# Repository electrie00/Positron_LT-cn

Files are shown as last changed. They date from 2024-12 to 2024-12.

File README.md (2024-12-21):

<div align="center">
  
# Positron LT-cn

<br>
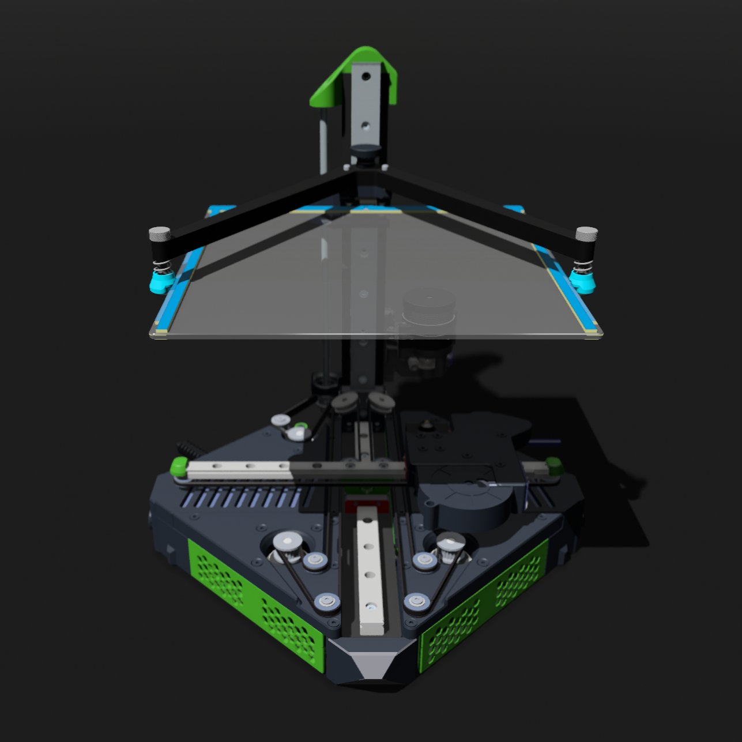
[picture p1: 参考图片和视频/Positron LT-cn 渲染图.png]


<br>

</div>

<br>

<br>

1. 国内可制造，任何零件均可在国内买到
2. 价格合理，目前价格大约在1500~2000元左右
3. 原版 LT 用户也可以很容易的升级这个版本，解决 LT 原版的问题
   
<br>

## - 改动点   （添加了部分 Positron V3.2 的新设计）： 

  1. **后惰轮张紧块** —— LT 原版的张紧块使用4个小惰轮倾斜安装，无法承受皮带张紧力，会被逐渐拉歪，最终导致皮带脱轨。 使用 V3.2 的设计两个大惰轮可以很好的解决这个问题，需要注意的是，V3.2 的惰轮是 CNC 做的，而此改版 LT 使用的是与 V3.2 参数相似成品惰轮，淘宝有卖

  2. **挤出机** —— LT 原版挤出机基于 BMG，我实际使用时有明显挤出不足的问题。使用 V3.2 的 Orbiter2.0 挤出机，仅修改了安装孔位，内部挤出结构与 v3.2 保持一致。 同时扩大了 RGB 灯孔位，以便折叠时刚好把挤出机卡入凹槽

  3. **热床接口** —— lt原版热床的磁吸接口强度不够，有时连接不稳，再加上 LT 原版热床支架的热床夹持结构不稳。整个热床可以说是摇摇欲坠。一旦磁吸接口虚接产生火花，就会导致热床接口损坏（ 亲身经历 ）。  使用 V3.2 的金手指连接接口，非常稳固。以及 V3.2 的热床支架，体积更小，夹持更稳，调平也更方便（ LT 原版的调平螺丝在下面，很别扭 ）。  需要注意的是，准确来说此改版lt仅使用了金手指接口，并没有 PCB，因此安装需要依赖胶水固定，以及接线需要做好绝缘，因为接线点与线轨金属滑块紧贴，容易短路

  4. **ITO 热床** —— ITO导电玻璃，整块玻璃均导电，发热更加均匀。两根长导线连接热床对边边缘作电极，分别连接 24V 正负极便可发热，中间区域是完全透明的整块玻璃。使用淘宝购买 ITO 玻璃加上可在嘉立创制作的 PCB，便可自制，这样就不用去国外买热床了，自己做的价格其实比淘宝的成品热床便宜。不建议使用淘宝的成品热床，那个并不是 ITO 热床，而是普通的导线粘贴在玻璃上。这个导线会干扰 Positron 的红外调平模块（ IR Probe ），导致有大量死区无法触发限位，影响 Z 归位以及网床探测

  5. **主体框架** —— 原版LT使用1010型材搭建框架，但这个在国内是买不到的，基本可以说没有办法。此改版 LT 修改为整体 CNC，价格还行 300 以内吧，这也是没有办法
  
  6. **皮带固定块** —— LT 原版的皮带固定块，仅仅靠设计的弯曲凹槽卡入皮带固定，也就是仅靠摩擦力固定，但凡皮带张紧一点，皮带便会脱落。而 V3.2 的皮带固定块改动太太，无法移植，并且 V3.2 的固定块设计也不算优秀。所以此改版 LT 在原版固定块基础上增加了 0.5mm 小孔，可以使用 0.5mm 的钢针插入，将皮带和固定块串在一起，就像串烧烤一样
     
<br>

## - 与 LT 版本和 V3.2 版本相比

 1. 用 CNC 解决了 LT 1010铝型材买不到的问题，同时添加了 V3.2 的新设计，也改进了大部分 LT 的 bug，使用体验大幅上升
 2. 比 V3.2 容易制造，至少不存在买不到特殊零件的问题了，并且是lt集成电源的,但体积就会比 V3.2 大一些。同时价格也比 V3.2便宜一倍
<br>

## - 注意

  1.此工程的文件仍在整理，文档依然还有许多没写
  
  2.此版本没有为打印机添加触摸屏幕，但保留了原版 LT 安装屏幕的孔位，有需要可以自己参考 LT 安装
  
  3. X，Y，Z 轴的步进电机依然不太好买，具体参数为 42 步进电机20mm厚15mm轴长。而我目前买的电机是 20mm 轴长，装上去才发现高了 5mm 会阻挡打印头移动，目前解决方案是在电机安装孔垫矮了 5mm，便可解决问题。其实也证明轴长 15~20mm 都是可以的，自行添加垫片调整高度即可

<br>

# 感谢Positron LT 和 Position 3D

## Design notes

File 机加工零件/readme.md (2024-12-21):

## 1~3 号文件只能 CNC 加工，嘉立创报价如下

1. Y轴 主梁               90.4元
2. Z轴 主梁               77.84元
3. Y轴-Z轴 折叠处连接块    49.38元
<br>

## 4 号文件按道理也应该 CNC 价格，嘉立创报价如下

4. 底部 X轴 横梁（两件）    93.93 * 2 = 187.86 元

#### 不过这个零件明明是最小的，单价却比前面的 CNC 零件都要贵，而且还需要两件。所以如果嫌贵的话，也可以使用3d打印塑料件替代，反正这两根梁不用承受很大的力，我也是3d打印的这两个零件
<br>

## 5 号文件需要7件，不过这个就不用 CNC 了，有更便宜的解决方法：去淘宝上随便找一家铁板激光切割定制的，将step或dwg图纸发过去，记得告知厚度1.5mm。参考单价如下

5. L形连接板 （七件）        18元

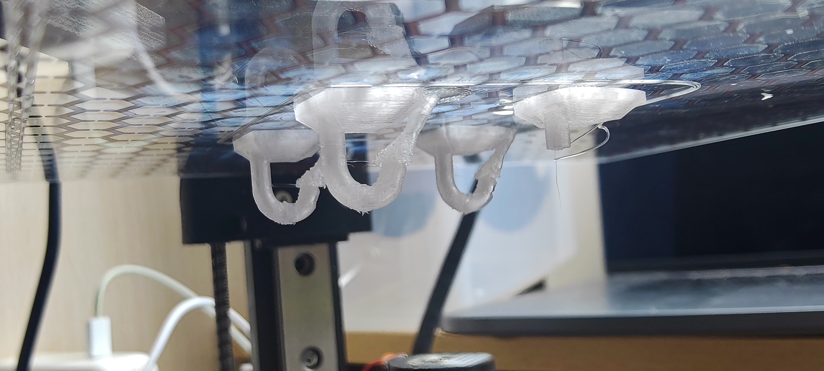
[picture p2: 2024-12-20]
参考图片和视频/透明petg 挂钩(1).jpg

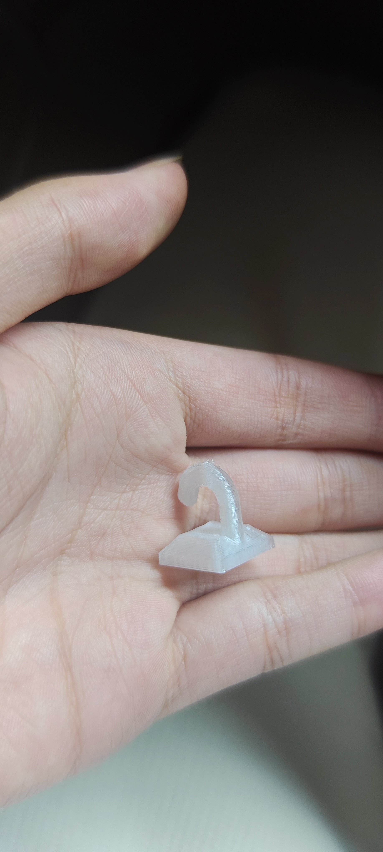
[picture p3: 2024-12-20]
参考图片和视频/透明petg 挂钩 (2).jpg

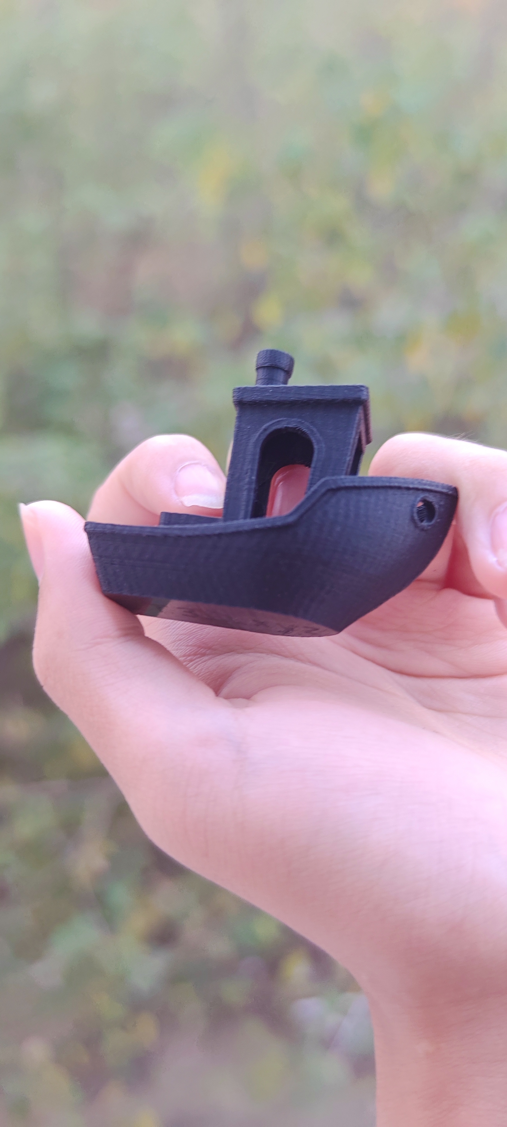
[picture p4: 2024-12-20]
参考图片和视频/测试小船.jpg

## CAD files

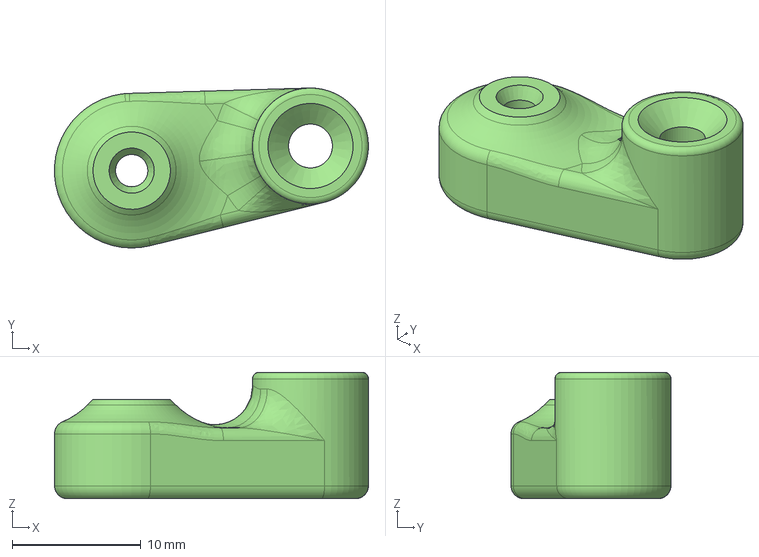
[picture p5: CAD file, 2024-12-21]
打印件/STEP/Z轴皮带张紧调节.step
24.4 x 12.4 x 9.80 mm

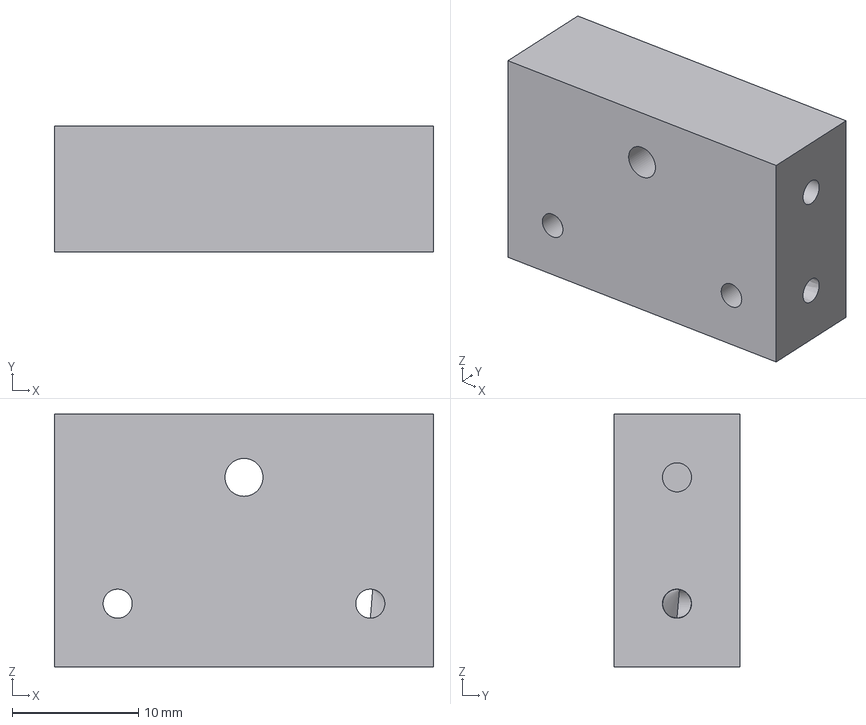
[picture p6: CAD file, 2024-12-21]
机加工零件/3. Y轴-Z轴 折叠处连接块.step
30.0 x 10.00 x 20.0 mm

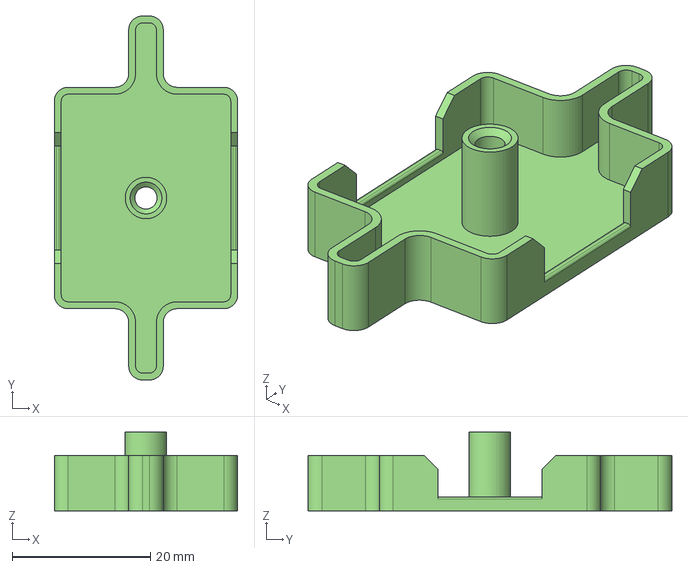
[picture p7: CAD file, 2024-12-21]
打印件/STEP/底盖打印件.step
26.5 x 52.6 x 11.4 mm

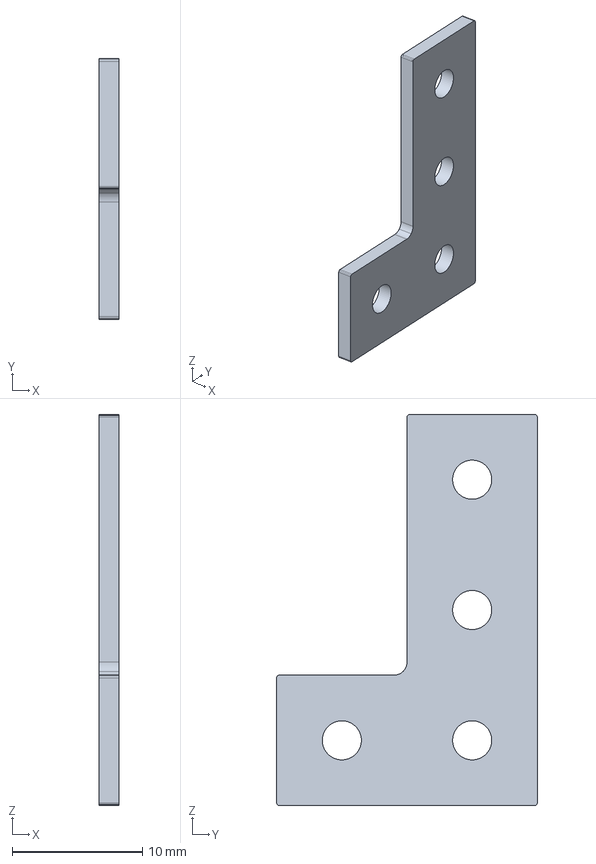
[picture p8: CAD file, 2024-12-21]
机加工零件/5. L形连接板（七件）.step
1.50 x 20.0 x 30.0 mm

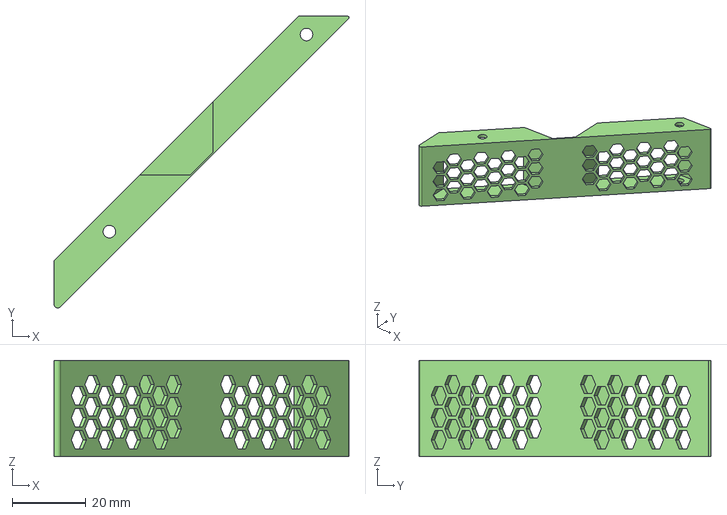
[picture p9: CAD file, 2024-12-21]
打印件/STEP/右装饰挡板.step
79.9 x 79.0 x 26.0 mm

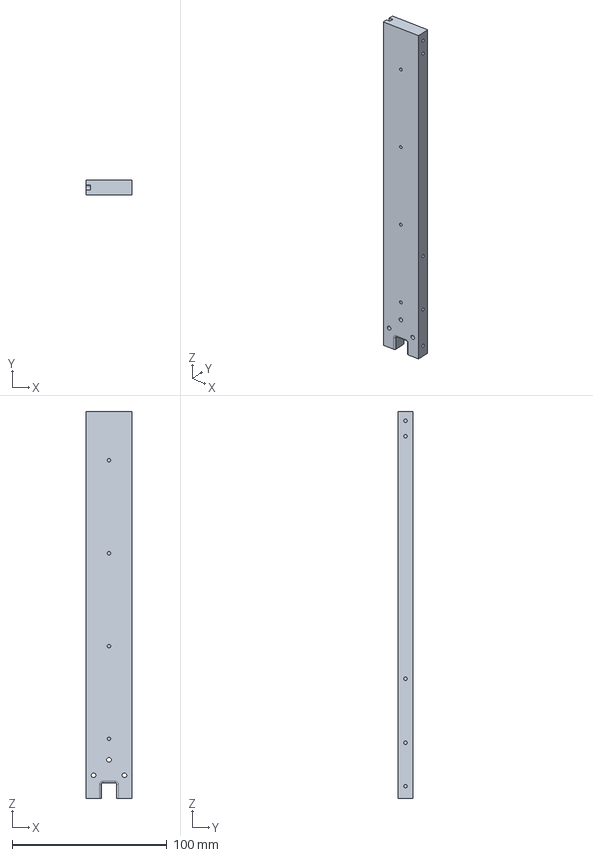
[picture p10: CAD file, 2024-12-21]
机加工零件/2. Z轴 主梁.step
30.0 x 10.0 x 250.0 mm

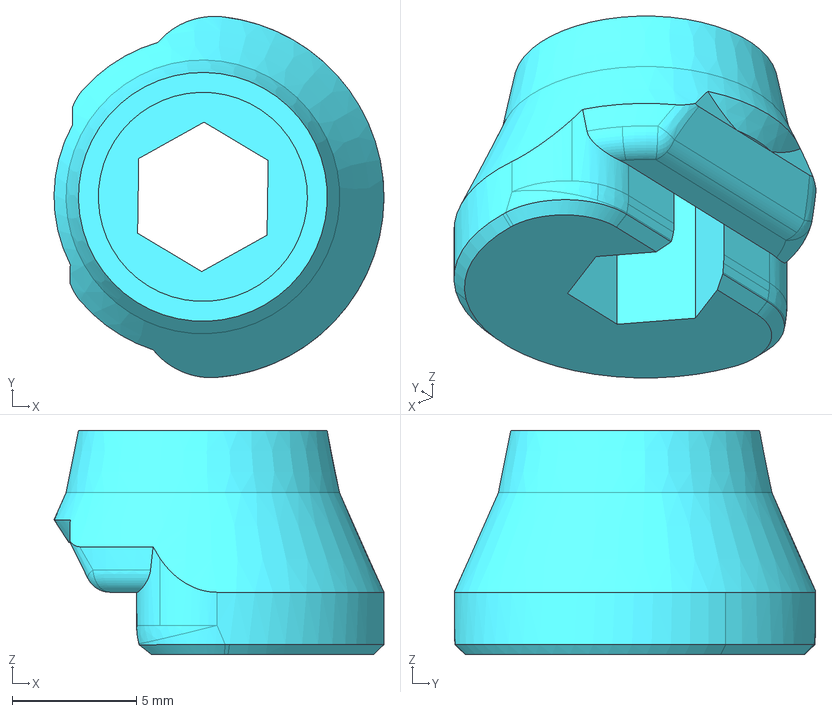
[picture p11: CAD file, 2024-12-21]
打印件/STEP/右端热床夹持打印件.step
13.3 x 14.5 x 9.00 mm

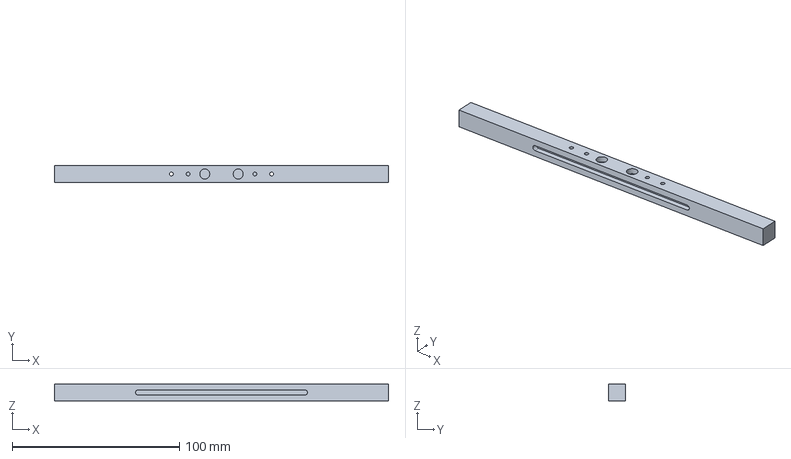
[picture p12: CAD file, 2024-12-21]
机加工零件/4. 底部 X轴 横梁（两件）.step
200.0 x 10.0 x 10.0 mm

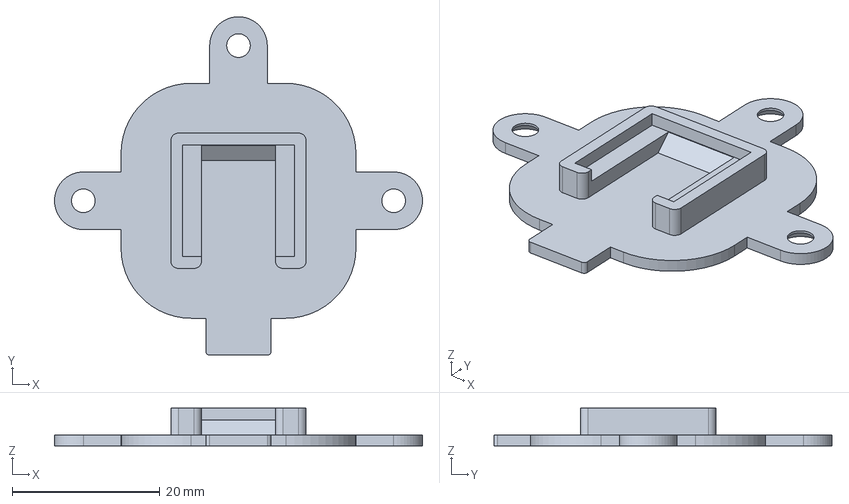
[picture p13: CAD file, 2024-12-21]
打印件/STEP/WS2812 RGB安装板.step
49.8 x 45.8 x 5.10 mm

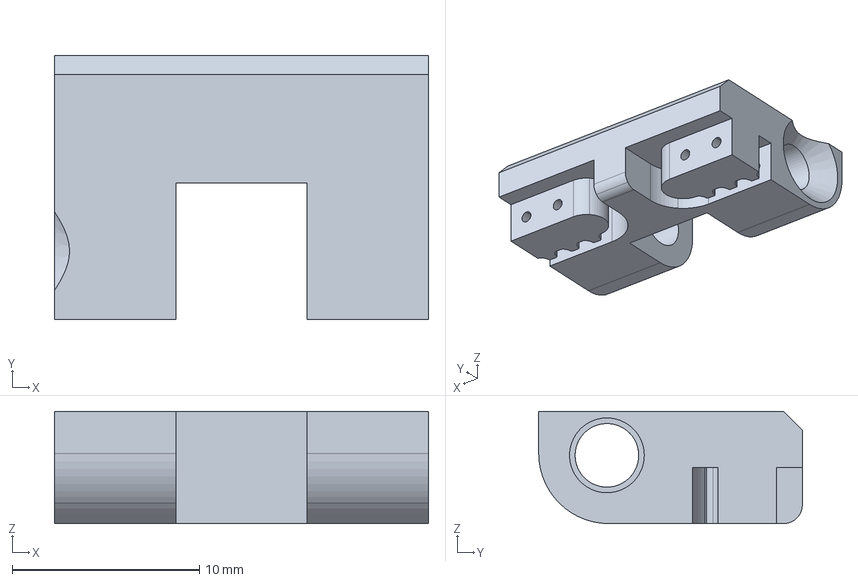
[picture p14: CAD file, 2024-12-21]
打印件/STEP/皮带固定块.step
20.0 x 14.1 x 6.00 mm

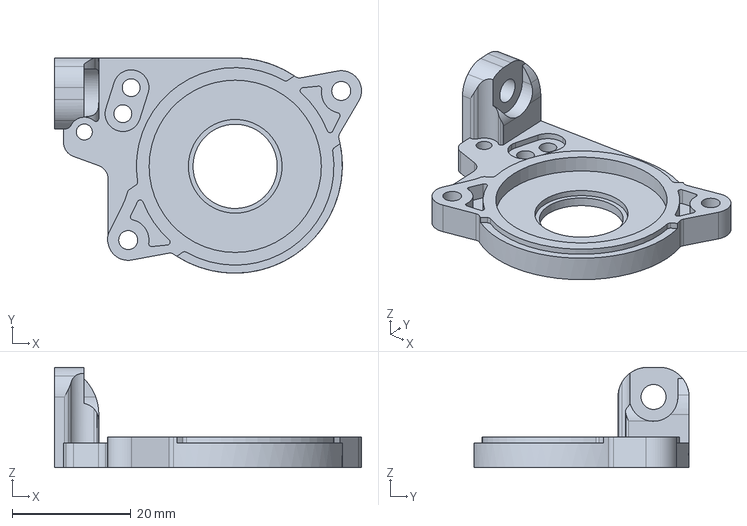
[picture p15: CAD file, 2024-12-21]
打印件/STEP/Orbiter2.0挤出机 Positron专用打印件（2）.step
51.8 x 36.3 x 16.9 mm

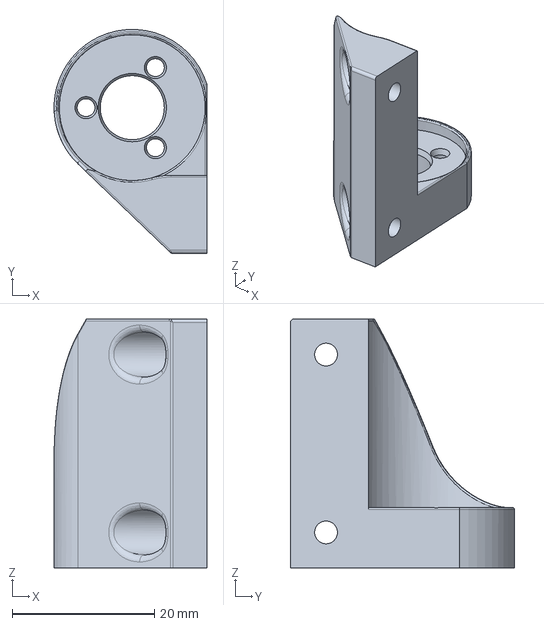
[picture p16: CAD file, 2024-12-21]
打印件/STEP/Z轴线轨-丝杆连接块.step
21.5 x 31.5 x 35.0 mm

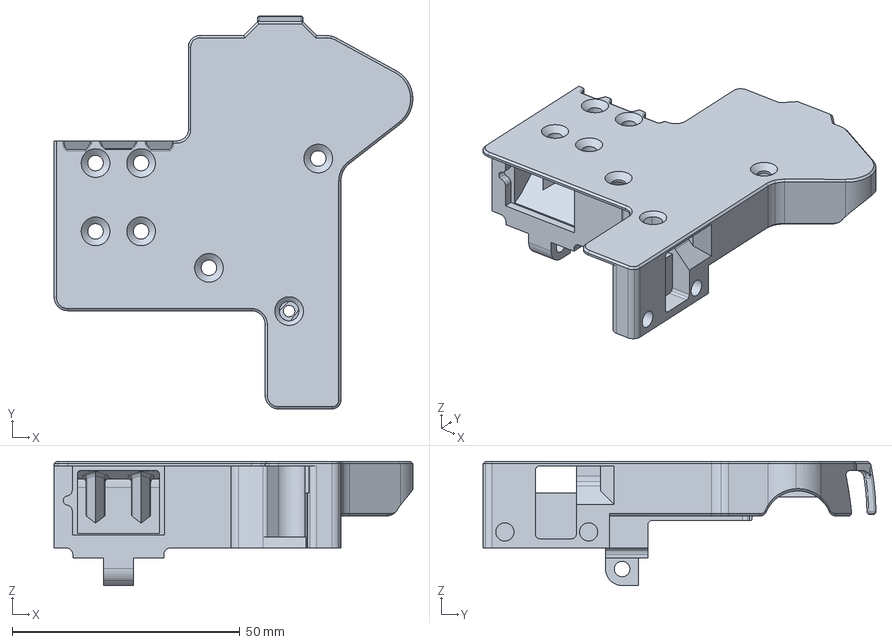
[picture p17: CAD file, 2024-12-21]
打印件/STEP/打印头主体打印件.step
78.8 x 86.3 x 27.3 mm

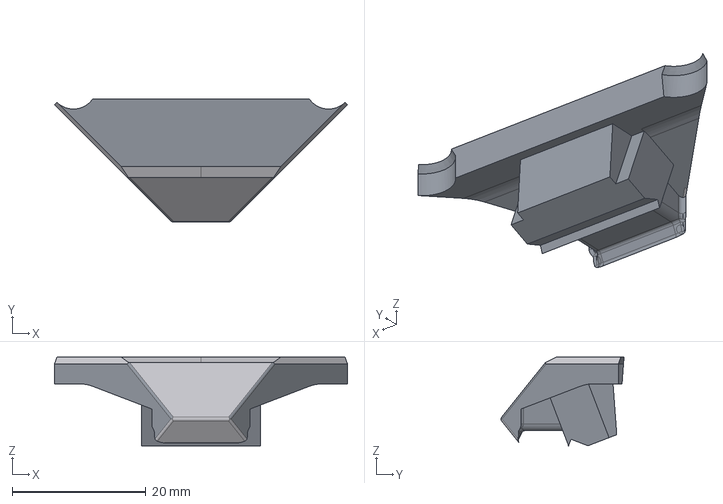
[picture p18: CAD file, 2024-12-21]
打印件/STEP/前端屏幕接口盖.step
43.9 x 18.4 x 13.3 mm

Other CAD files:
机加工零件/1. Y轴 主梁.step
打印件/STEP/左装饰挡板.step
打印件/STEP/Orbiter2.0挤出机 Positron专用打印件（1）.step
打印件/STEP/右半部分连接夹板.step
打印件/STEP/Orbiter2.0挤出机 Positron专用打印件（3）.step
打印件/STEP/Orbiter2.0挤出机 Positron专用打印件（4）.step
打印件/STEP/XY轴连接块 (1).step
打印件/STEP/X轴右端限位块.step
打印件/STEP/X轴左端限位块.step
打印件/STEP/Z轴丝杆-Z轴cnc主体连接件（上端）.step
打印件/STEP/Z轴丝杆-Z轴cnc主体连接件（下端）.step
打印件/STEP/skr pico主板绝缘底板框.step
打印件/STEP/前端打印件.step
打印件/STEP/右电机安装板.step
打印件/STEP/右电气仓上盖.step
打印件/STEP/右电气仓打印件.step
打印件/STEP/右风扇孔装饰盖.step
打印件/STEP/后端打印件.step
打印件/STEP/左半部分连接夹板.step
打印件/STEP/左电机安装板.step
打印件/STEP/左电气仓上盖.step
打印件/STEP/左电气仓打印件.step
打印件/STEP/左端热床夹持打印件.step
打印件/STEP/左风扇孔装饰盖.step
打印件/STEP/热床-Z轴连接块.step
打印件/STEP/热床V形支架.step
打印件/STEP/皮带张紧块.step
打印件/STL/Orbiter2.0挤出机 Positron专用打印件（1）.stl
打印件/STL/Orbiter2.0挤出机 Positron专用打印件（2）.stl
打印件/STL/Orbiter2.0挤出机 Positron专用打印件（3）.stl
打印件/STL/Orbiter2.0挤出机 Positron专用打印件（4）.stl
打印件/STL/WS2812 RGB安装板.stl
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

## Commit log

2024-12-20 上传CAD文件
2024-12-20 Rename lt 2.0 (1)-2024-12-20 002925.png to Positron LT-cn 渲染图.png
2024-12-20 上传参考图片和视频
2024-12-21 上传打印件和修改CAD
    [Orbiter2.0挤出机 Positron专用打印件（1）.step, Orbiter2.0挤出机 Positron专用打印件（1）.stl, Orbiter2.0挤出机 Positron专用打印件（2）.step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]
2024-12-21 调整文件夹
2024-12-21 上传文件
    [L形连接板.step, Orbiter2.0挤出机 Positron专用打印件（1）.step, Orbiter2.0挤出机 Positron专用打印件（1）.stl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]
2024-12-21 修改文件名
    [1. Y轴 主梁.step, 2. Z轴 主梁.step, 3. Y轴-Z轴 折叠处连接块.step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]
2024-12-21 添加说明
    [4. 底部 X轴 横梁（两件）.step, 5. L形连接板（七件）.dwg, 5. L形连接板（七件）.step]
